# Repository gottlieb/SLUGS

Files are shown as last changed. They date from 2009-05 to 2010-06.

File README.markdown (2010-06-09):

1. Introduction
===============

The Santa Cruz Low-cost UAV GNC System is a high-end UAV Autopilot that has been developed by the Autonomous Systems Lab at the University of California Santa Cruz. It has been thoroughly tested in flight.

SLUGS Official  Website <http://slugsuav.soe.ucsc.edu/>.

The SLUGS Autopilot offers the following features:

* Designed from the ground-up to be easily reprogrammable using Mathworks' Simulink and The Real Time Workshop Embedded Coder.

* Powered by two dsPICs DSCs; one for sensor fusion and attitude estimation from a rich sensor suite. The other for control and communications tasks, providing enough processing power for complex algorithms.

* Small enough to fit in a tactical UAV but able to drive up to ten different servos. It also includes a multiplexer to choose between pilot and automatic control

* Easily go from Simulink simulation to Embedded code. Test your algorithms in Simulink then download them to the Autopilot without any effort.

* Fast execution time. The main processing cycles are executed at 100Hz. Telemetry reports of attitude and position at 100 Hz and the rest of the messages scheduled at 10 Hz.

* Fully integrated with Google Earth to allow the Ground Station operator to create flight way points and display the UAV's flight trajectory in 3D.

* Full featured Ground Station software with graphical displays for all of the UAV telemetry. More than 15 different telemetry sentences to report the full status of the UAV.

* Complete Hardware-In-the-Loop simulator allows you to test new algorithms directly in the auto pilot without leaving your desk. No more waiting for flying to test new ideas.

* Very low power allows to run on a typical RC battery for extended time. You can select to power the receiver and MUX from the same battery, or use an additional battery via configuration jumpers.

* Open. Hardware schematics, layout, and software source code available via a GIT repository with an MIT Open Source License.

2. Code and Hardware
====================

This section will guide you to get the complete repository to your hard drive. If you don't know what GIT is, you can of course read about it in the Wikipedia. This is a small screencast that was prepared for UCSC's Autonomous Systems Lab.

msysgit
--------

Using msysgit is the best way to get Git running on Windows. Git is officially supported under Cygwin, but I consider using it this way more of a hack and I also don't want to install all of Cygwin just for this (takes forever mostly). msysgit can be installed by downloading it from here. Make sure you select the plain Git installation, not the portable or msysgit versions. This is currently at version 1.6.5.1.

There are no surprises during the installation save one set of options. In order for msysgit to work properly with Tortoise Git you must select the option to add Git to the system PATH environment variable (this was the middle option in version 1.6.3).

Once you have msysgit running than all you have to do is open a git bash window (right click on the selected folder on the Windows explorer and select git bash here) and then type:

git clone git://github.com/malife/SLUGS.git

Tar or Zip File
---------------

If you only want a copy of the files and are not interested on getting all the benefits of GIT you can go to the github project page <http://github.com/malife/SLUGS>  and download a zip or tar file of the selected branch by clicking on the `download` button located in the top right corner.

3. Requirements
===============

Software Requirements
---------------------

These are the software requirements to get up and running. Note that if you do not plan on modifying any of the sections you do not need the requirements since we provide binaries for all of the sections. I.E. if you do not want to modify the Ground Station, then you do not need the components listed under that section.
Ground Station 

* Borland C++ Builder 6.0 (old version but very reliable. Yes, hard to find)
* RX Lib for C++ Builder Components (Free)
* Overbyte ICS UDP Components (Free)
* Abakus VCL for graphical components (Commercial)
* Tiny XML for interacting with KML files from Google Earth
* Simulink Models

* Matlab 2007A or newer with Simulink, the Real Time Workshop, and the Embedded Coder
* dsPIC Blockset
* Schematics and Layout

* Version 1 of the board is in Eagle 4.0
* Version 2 of the board in Orcad
* Microchip dsPIC Software and Hardware

* C30 Compiler Student Edition (free)
* PicKit 2 Programmer and Debugger (or any other dsPIC programmer)

Repository Organization
-----------------------
The main Simulink models for each of the DSCs lie in the repository's root directory, they are aptly named ControlMCUSlugsMKII and SensorMCUSlugsMKII. Additionally the repository also includes HEX files of each model.

The root directory also contains an init script (`mcuInit.m`) and a Simulink Library with the most commonly used blocks (`SLUGS_Library.mdl`).

There are eight subdirectories, each with its own README file:

* **Calibration**: It contains all the m-files to produce the magnetometer and accelerometer calibration numbers based on collected data sets. It also contains the temperature compensation scripts.
* **clib**: Contains all the C-files used by Simulink
* **DataSamples**: Self explanatory
* **FlightData**: It contains a script to analyze the collected data from a telemtry file. It also contains a Simulink model to replay the telemetry file.
* **GroundStation**: It contains all the source code of the ground station software.
* **hardware**: It contains all the source, PDFs and Gerbers of the hardware.
* **HILSim**: It contains the Simulink file used for the HIL Simulator.
* **InnerOuterLoop**: It contains the main Simulink file to run software simulation, whic includes a full 6DOF model of the Rascal UAV, the inner and outer loop. It also contains some scripts to analyze the data after every simulation. 

It is important to note that the repository includes a `.gitattributes` file which is used to make Git treat the Simulink model files as binaries (even though they are really text files). This facilitates handling of the MDL files but the tradeoff is that it makes contributions harder. 

Sending a Board to Manufacture
------------------------------

Building a Connection Harness
-----------------------------

(Comment: Remember to point out that the PIC12 should be preprogrammed. Jonathan Lowert)

Flight Harness
--------------

Ground Harness
--------------

Understanding the Architecture
------------------------------

How to Contribute
-----------------

4. Installing Hardware to the UAV

5. Software Simulation

6. Hardware in the Loop Simulation

7. References

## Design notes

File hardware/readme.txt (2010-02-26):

"full_slugs2_and_2_1_with_all_library_pads" contains the full zipped project, library, and padstacks. It contains more files than necessary because I don't want to miss anything. It should work fine.

"board_gerber_files" has the files you need to submit to a board house. It also has some screen shots I made while test-submitting to Sierra Proto Express No-Touch.

"PDFs" has the schematics in PDF form, duh

"link_board" is an Altium Designer 09 project containing schematics for the link board. This board sits between the Xtend radio and the groundstation laptop and acts as a go-between.

Enjoy!

-Greg Horn
August 30, 2009

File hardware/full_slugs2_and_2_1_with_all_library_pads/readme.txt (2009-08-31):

Extract symbols.rar and merge contents with:

C:\OrCAD\OrCAD_16.0\share\pcb\pcb_lib

for library padstacks to work. Override files if necessary.

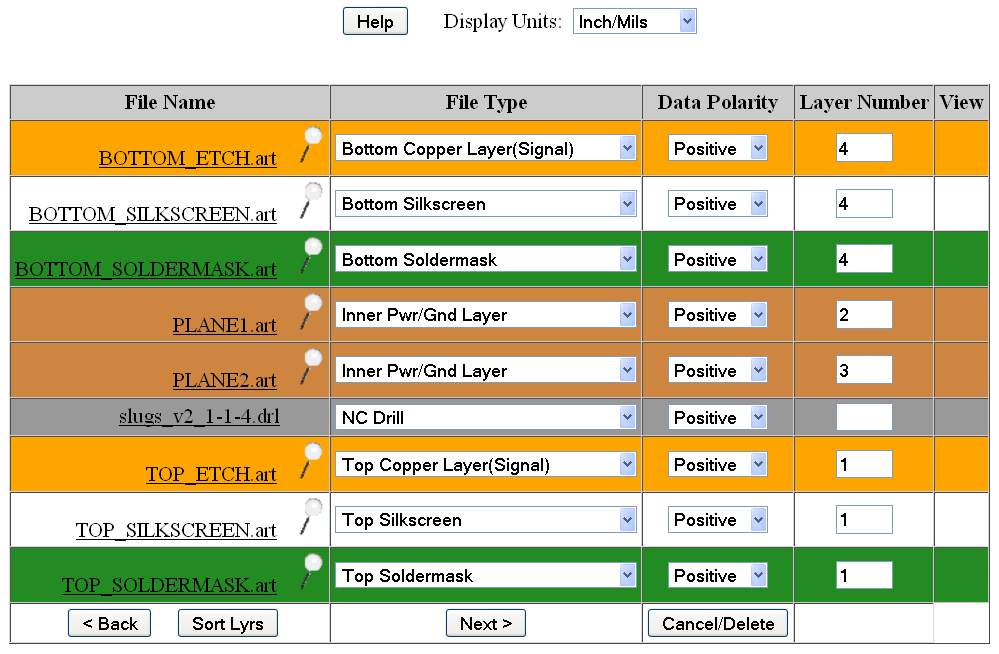
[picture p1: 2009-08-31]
hardware/board_gerber_files/layer_info.bmp

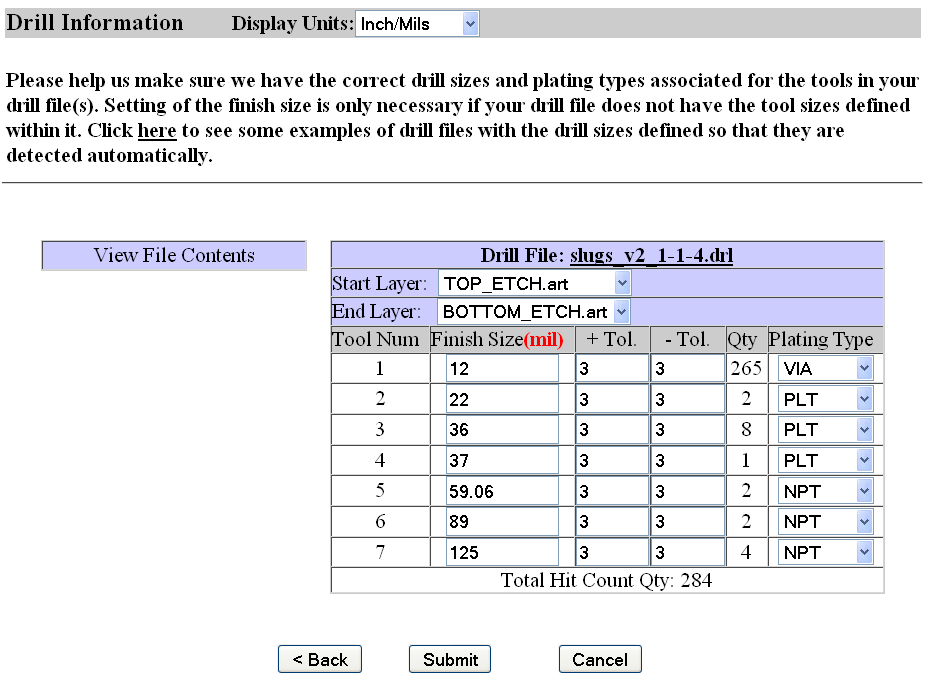
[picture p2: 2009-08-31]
hardware/full_slugs2_and_2_1_with_all_library_pads/SLUGS_V2/allegro_slugs2.1/board_files/drill_info.bmp

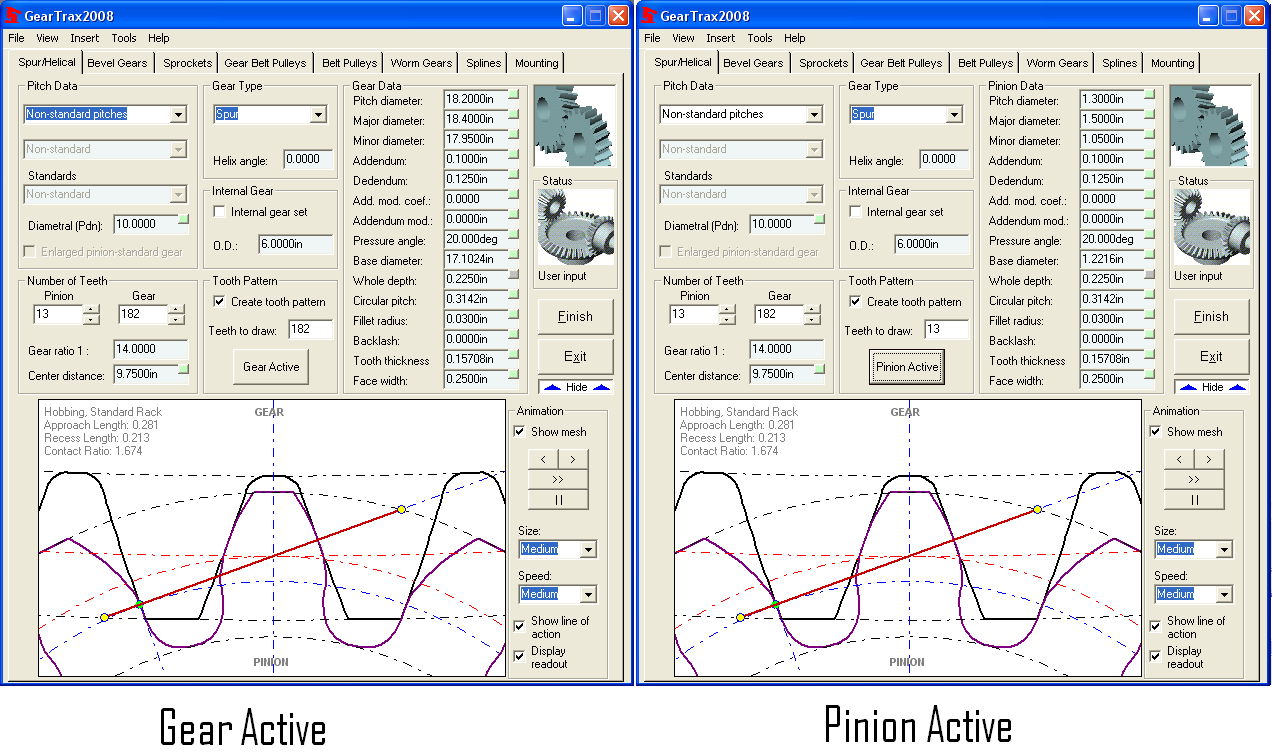
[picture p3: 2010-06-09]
hardware/Rotation Table v3/Gear Specs.bmp

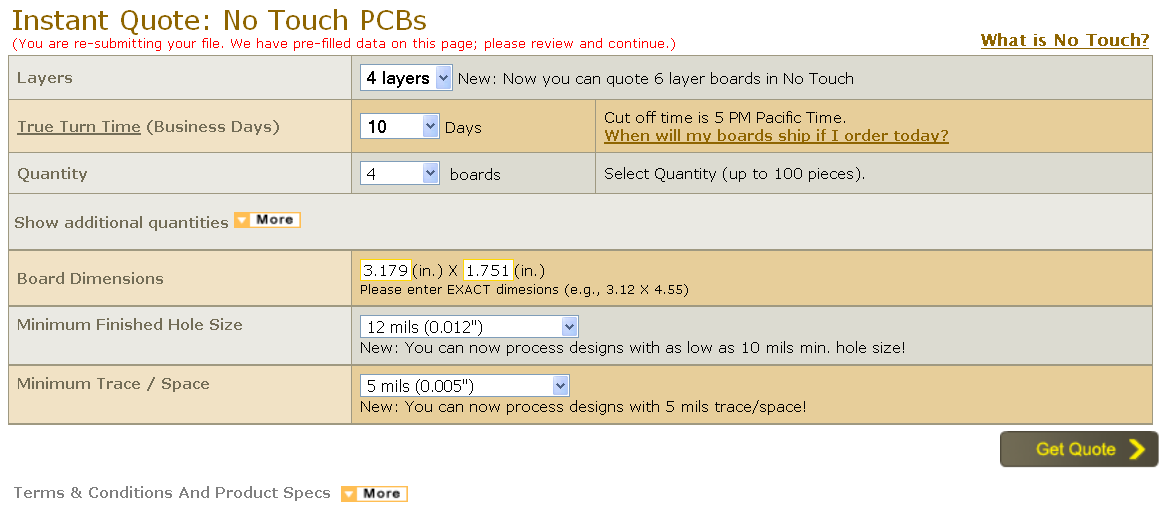
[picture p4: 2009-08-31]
hardware/board_gerber_files/sierra_no_touch_specs.bmp

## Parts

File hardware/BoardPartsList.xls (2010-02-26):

UCSC
BOM: SLUGS 2.1 |  |  |  |  |  |  |  | DNA11120
Date: 11/04/2009 BOM SENT TO THE CUSTOMER
 |  |  |  |  |  |  |  |  |  |  |  |  | N=
Item | SPE part # | Qty/ bd | Reference desig. | Customer part # | Value | Footprint | Voltage Rating | Description / Extended specs | Mnfr or vendor description/ specs | Manfr. | Manf part # | Distributor | Distributor P/N | ASSEMBLY / PROCUREMENT REMARKS | Customer Comments | Alternate Given by customer
1 |  | 34 | C1,C2,C3,C4,C5,C6,C7,C8,C9,C10,C11,C12,C13,C14,C17,C18,C19,C22,C30,C31,C32,C33,C34,C35,C54,C55,C56,C64,C65,C66,C67,C68,C69,C70 |  | .1u | C0603 | 16V |  | CAP .10UF 16V CERAMIC X7R 0603 | Kemet | C0603C104J4RACTU | DIGIKEY | 399-1097-1-ND
2 |  | 10 | C15,C16,C37,C40,C41,C44,C46,C47,C50,C53 |  | 10u | C0805 | 16V |  | CAP CER 10UF 16V X5R 0805 | Taiyo Yuden | EMK212BJ106KG-T | DIGIKEY | 587-1295-1-ND | Ship Date Estimate (mm/dd/yyyy) 1/7/2010 | Replace by alternate | 311-1142-1-ND
3 |  | 7 | C20,C23,C24,C25,C27,C28,C57 |  | 1u | C0603 | 10V |  | CAP 1UF 10V CERAMIC 0603 X5R | Panasonic - ECG | ECJ-1VB1A105K | DIGIKEY | PCC2174CT-ND
4 |  | 1 | C26 |  | 1n | C0603 | 50V |  | CAP 1000PF 50V CERAMIC X7R 0603 | Panasonic - ECG | ECJ-1VB1H102K | DIGIKEY | PCC1772CT-ND
5 |  | 1 | C29 |  | 22u | C1206 |  | 10V (-20%,+80% value tolerance OK) | CAP 22UF 10V CERAMIC F 1206 | Panasonic - ECG | ECJ-3YF1A226Z | DIGIKEY | PCC2236CT-ND
6 |  | 0 | C36,C38 |  | 220u | SMD_CAP_10x10_5 | 25V |  | CAP 220UF 35V ELECT HA SMD | Panasonic - ECG | EEV-HA1V221P | DIGIKEY | PCE3226CT-ND
6 |  | 2 | C36,C38 |  | 220u | SMD_CAP_10x10_5 | 25V |  | CAP 220UF 35V ELECT HA SMD | Panasonic - ECG | EEE-HA1V221P | DIGIKEY | PCE4241CT-ND
7 |  | 1 | C39 |  | 10u,20V | C1206 | 20V |  | CAP TANT 10UF 20V 20% SMD | Kemet | T491A106M020AT | DIGIKEY | 399-5152-1-ND
8 |  | 1 | C49 |  | 4u7 | C0805 | 10V |  | CAP TANTALUM 4.7UF 10V 10% SMD | AVX Corporation | TAJR475K010RNJ | DIGIKEY | 478-3280-1-ND
9 |  | 1 | C52 |  | .22u | C0603 | 16V |  | CAP .22UF 16V CERAMIC Y5V 0603 | Panasonic - ECG | ECJ-1VF1C224Z | DIGIKEY | PCC1790CT-ND
10 |  | 1 | C58 |  | .01u | C0603 | 16V |  | CAP 10000PF 16V CERM X7R 0603 | Panasonic - ECG | ECJ-1VB1C103K | DIGIKEY | PCC1750CT-ND
11 |  | 1 | C59 |  | 2u2 | C0805 | 10V |  | CAP TANTALUM 2.2UF 10V 20% SMD | Rohm Semiconductor | TCFGP1A225M8R | DIGIKEY | 511-1490-1-ND
12 |  | 1 | C60 |  | 470p | C0603 | 50V |  | CAP CERAMIC 470PF 50V NP0 0603 | Panasonic - ECG | ECJ-1VC1H471J | DIGIKEY | PCC2147CT-ND
13 |  | 1 | C61 |  | 47p | C0603 | 50V |  | CAP CERAMIC 47PF 50V NP0 0603 | Yageo | CC0603JRNP09BN470 | DIGIKEY | 311-1065-1-ND
14 |  | 2 | C62,C63 |  | .47u | C0603 | 16V |  | CAP TANT .47UF 16V 10% 0603 | AVX Corporation | TACL474K016RTA | DIGIKEY | 445-1277-1-ND
15 |  | 2 | D1,D2 |  | 1N4148WT | diode_sod523 |  |  | DIODE SWITCH 100V 150MW SOD-523 | Diodes Inc | 1N4148WT-7 | DIGIKEY | 1N4148WTDICT-ND
16 |  | 10 | D5,D6,D7,D8,D9,D10,D11,D12,D13,D14 |  | LED0603 Green | D0603 |  |  | LED 0603 ULTRA BRIGHT GRN 35MCD | Vishay/Semiconductors | TLMG1100-GS08 | DIGIKEY | 751-1165-1-ND
17 |  | 1 | D15 |  | DIODE | dio400 |  |  | DIODE STD REC 1A 50V DO41 | ON Semiconductor | 1N4001RLG | DIGIKEY | 1N4001RLGOSCT-ND
18 |  | 1 | J1 |  | connector_60 | AMPMODU50_60_rightangle |  |  | CONN HEADER 60POS .050" R/A GOLD | Tyco Electronics | 5-104069-7 | DIGIKEY | A31870-ND
19 |  | 2 | J2,J3 |  | GND | jumper2 |  |  |  |  |  |  |  | Ignore. DO NOT MOUNT
20 |  | 1 | J6 |  | BATT | screw_terminal |  |  | TERM BLOCK 2POS SIDE ENT 2.54MM | Tyco Electronics | 282834-2 | DIGIKEY | A98333-ND
21 |  | 1 | R1 |  | 120 | R0603 |  | All resistors 1%, 1/10 watt. | RES 120 OHM 1/10W 1% 0603 SMD | Rohm Semiconductor | MCR03EZPFX1200 | DIGIKEY | RHM120HCT-ND
22 |  | 1 | R2 |  | 120/OPT | R0603 |  |  |  |  |  |  |  | DO NOT MOUNT
23 |  | 2 | R3,R4 |  | 4k7 | R0603 |  |  | RES 4.70K OHM 1/10W 1% 0603 SMD | Rohm Semiconductor | MCR03EZPFX4701 | DIGIKEY | RHM4.70KHCT-ND
24 |  | 2 | R5,R6 |  | 47k | R0603 |  |  | RES 47.0K OHM 1/10W 1% 0603 SMD | Rohm Semiconductor | MCR03EZPFX4702 | DIGIKEY | RHM47.0KHCT-ND
25 |  | 4 | R7,R24,R31,R32 |  | 200 | R0603 |  |  | RES 200 OHM 1/10W 1% 0603 SMD | Rohm Semiconductor | MCR03EZPFX2000 | DIGIKEY | RHM200HCT-ND
26 |  | 4 | R9,R11,R12,R16 |  | 750 | R0603 |  |  | RES 750 OHM 1/10W 1% 0603 SMD | Rohm Semiconductor | MCR03EZPFX7500 | DIGIKEY | RHM750HCT-ND
27 |  | 8 | R10,R13,R14,R15,R17,R18, R19,R20 |  | 5k | R0603 |  |  | RES 4.99K OHM 1/10W 1% 0603 SMD | Rohm Semiconductor | MCR03EZPFX4991 | DIGIKEY | RHM4.99KHCT-ND
29 |  | 1 | R21 |  | 100 | R0603 |  |  | RES 100 OHM 1/10W 1% 0603 SMD | Rohm Semiconductor | MCR03EZPFX1000 | DIGIKEY | RHM100HCT-ND
30 |  | 1 | R22 |  | 13k1,1% | R0603 |  |  | RES 13.0K OHM 1/10W 1% 0603 SMD | Rohm Semiconductor | MCR03EZPFX1302 | DIGIKEY | RHM13.0KHCT-ND
31 |  | 1 | R23 |  | 330k | R0603 |  |  | RES 330K OHM 1/10W 1% 0603 SMD | Rohm Semiconductor | MCR03EZPFX3303 | DIGIKEY | RHM330KHCT-ND
32 |  | 1 | R25 |  | 10k | R0603 |  |  | RES 10.0K OHM 1/10W 1% 0603 SMD | Panasonic - ECG | ERJ-3EKF1002V | DIGIKEY | P10.0KHCT-ND
33 |  | 2 | R26,R28 |  | 17k | R0603 |  |  | RES 16.9K OHM 1/10W 1% 0603 SMD | Panasonic - ECG | ERJ-3EKF1692V | DIGIKEY | P16.9KHCT-ND
34 |  | 1 | R27 |  | 3k3 | R0603 |  |  | RES 3.30K OHM 1/10W 1% 0603 SMD | Rohm Semiconductor | MCR03EZPFX3301 | DIGIKEY | RHM3.30KHCT-ND
35 |  | 2 | R29,R30 |  | 34k | R0603 |  |  | RES 34.0K OHM 1/10W 1% 0603 SMD | Rohm Semiconductor | MCR03EZPFX3402 | DIGIKEY | RHM34.0KHCT-ND
36 |  | 2 | U1,U2 |  | dsPIC33FJ256MC710PT | TQFP100_12x12MC |  |  | IC DSPIC MCU/DSP 256K 100TQFP | Microchip Technology | DSPIC33FJ256MC710-I/PT | DIGIKEY | DSPIC33FJ256MC710-I/PT-ND
37 |  | 2 | U3,U5 |  | SN65HVD230D | d8 |  |  | IC CAN TRANSCEIVER 3.3V 8-SOIC | Texas Instruments | SN65HVD230D | DIGIKEY | SN65HVD230D-ND
38 |  | 1 | U4 |  | ECS2033 | ECS2033 |  |  | OSC 12.000 MHZ 3.3V SMD | ECS Inc | ECS-2033-120-BN | DIGIKEY | XC1426CT-ND
39 |  | 1 | U6 |  | MCP9700 | sot23 |  |  | IC SENSOR THERMAL 2.3V SOT23-3 | Microchip Technology | MCP9700T-E/TT | DIGIKEY | MCP9700T-E/TTCT-ND
40 |  | 1 | U7 |  | 74CBTLV16210 | DGV48 |  |  | IC LV 20-BIT FET BUS SW 48-TVSOP | Texas Instruments | SN74CBTLV16210VR | DIGIKEY | 296-6498-1-ND
41 |  | 0 | U8 |  | MAX3223E | MAX3223EETP |  |  | IC TXRX RS232 250KBPS SD 20-TQFN | Maxim Integrated Products | MAX3223EETP+ | DIGIKEY | MAX3223EETP+-ND
41 |  | 1 | U8 |  | MAX3223E | MAX3223EETP |  |  | IC TXRX RS232 250KBPS SD 20-TQFN | Maxim Integrated Products | MAX3223EETP+ | Maxim Integrated Products | MAX3223EETP+
42 |  | 1 | U9 |  | PIC12F683-XSN | SOIC8-N_MC |  |  | IC MCU FLASH 2KX14 8SOIC | Microchip Technology | PIC12F683-I/SN | DIGIKEY | PIC12F683-I/SN-ND
43 |  | 1 | U10 |  | ptn78000waz | EUT5 |  |  | REG SW 2.5-12.6V 1.5A SMD | Texas Instruments | PTN78000WAZ | DIGIKEY | 296-20508-ND
44 |  | 2 | U11,U12 |  | LP38690SD-3.3 | SDE06A-L |  |  | IC REG LDO 1A 3.3V 6-LLP | National Semiconductor | LP38690SD-3.3/NOPB | DIGIKEY | LP38690SD-3.3CT-ND
45 |  | 1 | U13 |  | LP2986AIMM | MUA08A-L |  |  | IC REG LDO 5V 200MA 8-MSOP | National Semiconductor | LP2986AIMM-5.0/NOPB | DIGIKEY | LP2986AIMM-5.0CT-ND
46 |  | 0 | U14 |  | ADIS16350AMLZ | ADIS16350 |  |  | MOD TRI-AXIS GYRO/ACCEL 24-LEAD | Analog Devices Inc | ADIS16350AMLZ | DIGIKEY | ADIS16350AMLZ-ND
46 |  | 1 | U14 |  | ADIS16350AMLZ | ADIS16350 |  |  | MOD TRI-AXIS GYRO/ACCEL 24-LEAD | SAMTEC | CLM-112-02-L-D | SAMTEC | CLM-112-02-L-D
47 |  | 1 | U15 |  | HMC5843 | HMC5843 |  |  | SENSOR MAGNETIC 3 AXIS 20-LCC | Honeywell Microelectronics & Precision Sensors | HMC5843 | DIGIKEY | 342-1071-ND
48 |  | 1 | U16 |  | LMV844MT | MTC14-L |  |  | IC OP AMP RRIO CMOS INP 14-TSSOP | National Semiconductor | LMV844MT/NOPB | DIGIKEY | LMV844MT-ND
49 |  | 1 | U17 |  | MPXH6115A6U_6T1 | MPXH6115A6U_6T1 |  |  | SENSOR ABS PRESS 16.7PSI MAX | Freescale Semiconductor | MPXH6115A6U | DIGIKEY | MPXH6115A6U-ND
50 |  | 1 | U18 |  | MPXV5004DP | MPXV5010DP |  |  | SENSOR PRESSURE SMD 8-SOP | Freescale Semiconductor | MPXV5004DP | DIGIKEY | MPXV5004DP-ND
51 |  | 1 |  |  |  |  |  | PCB manufactured by SPE |  |  |  |  |  | PCB
 |  | 131 | total # of components
 |  | 140 | Total # of compnents to be assembled
 |  | 1 | total # of DNP components
 |  | 3 | total # of DIP components to be Assembled
 |  | 137 | total # of SMD components to be Assembled

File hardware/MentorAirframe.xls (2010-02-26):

Price List
Description | Qty | Price | Total | Web Page
Multiplex Mentor | 2 | 147.99 | 295.98 | http://www3.towerhobbies.com/cgi-bin/wti0001p?&I=LXVEP7
Multiplex Mentor servo pack | 2 | 69.9 | 139.8 | http://www3.towerhobbies.com/cgi-bin/wti0001p?&I=LXVEP9&P=M
Phoenix 60 ESC | 2 | 118.99 | 237.98 | http://www3.towerhobbies.com/cgi-bin/wti0001p?&I=LXGVS3&P=FR
Castle Creations Link Programming Kit | 1 | 21.99 | 21.99 | http://www3.towerhobbies.com/cgi-bin/wti0001p?&I=LXGVR8&P=7
Himax 3528-1000 Mentor Motor | 2 | 147.99 | 295.98 | http://www3.towerhobbies.com/cgi-bin/wti0001p?&I=LXVEP8&P=M
APC 11 x 7 Sport Propeller | 5 | 2.79 | 13.95 | http://www3.towerhobbies.com/cgi-bin/wti0001p?&I=LX1558&P=M
WS Deans 2-pin Ultra Plug | 15 | 3.09 | 46.35 | http://www3.towerhobbies.com/cgi-bin/wti0001p?&I=LXKX39&P=M
CA+ Glue | 2 | 6.99 | 13.98 | http://www3.towerhobbies.com/cgi-bin/wti0001p?&I=LXK287&P=ML
Spektrum DX7 with AR7000 | 1 | 349.99 | 349.99 | http://search.horizonhobby.com/index.jsp?N=0&Ntt=dx7&sid=126B91FA82E5
Thunder Power 1350 ma 3-cell Pro Lite V2 | 3 | 34.99 | 104.97 | http://www.horizonhobby.com/Products/Default.aspx?ProdID=THP13503SPL2
Thunder Power 5000ma 3-cell Pro Power | 3 | 129.99 | 389.97 | http://www.horizonhobby.com/Products/Default.aspx?ProdID=THP50003SP30
Spektrum AR7000 DSM2 | 1 | 99.99 | 99.99 | http://www.horizonhobby.com/Products/Default.aspx?ProdID=SPM6070
Thunder Power LiPo Charger and Balancer | 1 | 99.99 | 99.99 | http://www.horizonhobby.com/Products/Default.aspx?ProdID=THP610
 |  |  | 0
 |  |  | 0
 |  |  | 0
 |  |  | 0
 |  |  | 0
 | TOTAL |  | 2110.92

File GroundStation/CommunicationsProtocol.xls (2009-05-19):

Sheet: Sentence Structure
SYNC1 | SYNC2 | TYPE | LENGTH | PAYLOAD |  |  |  | EOM1 | EOM2 | CHKSM | General Structure
$ | @ | 1 | 27 | 80 | 1 | … | 35 | * | @ | 241 | Sample Sentence
 |  |  |  |  |  |  |  |  |  |  |  |  |  | 201
Message Identifiers |  |  |  |  |  |  |  |  |  |  |  | Memory Locations
Type | Payload Length | Contents |  |  |  |  |  |  |  | Update Freq. |  | Address | Contents | Message
SENSOR MCU GENERATED SENTENCES |  |  |  |  |  |  |  |  |  |  |  | 0 | PID 1 P Gain | PID Longitudinal Gains
1 | 27 | GPS Data from Messages GPRMC and GPGGA |  |  |  |  |  |  |  | 10 |  | 2 | PID 1 I Gain
2 | 4 | MCU Status: Load, Vdetect, Battery Status |  |  |  |  |  |  |  | 10 |  | 4 | PID 1 D Gain
3 | 18 | Raw sensor reading from the sensors |  |  |  |  |  |  |  | 10 |  | 6 | PID 2 P Gain
4 | 24 | Attitude Estimation from Kalman Filter |  |  |  |  |  |  |  | 100 |  | 8 | PID 2 I Gain
5 | 10 | Dynamic and Static Pressure, Temperature |  |  |  |  |  |  |  | 10 |  | 10 | PID 2 D Gain
6 | 24 | Sensor Bias |  |  |  |  |  |  |  | 10 |  | 12 | PID 3 P Gain
7 | 18 | Diagnostic Message |  |  |  |  |  |  |  | 10 |  | 14 | PID 3 I Gain
8 |  | Vacant |  |  |  |  |  |  |  |  |  | 16 | PID 3 D Gain
9 | 10 | Pilot Console Commands |  |  |  |  |  |  |  | 10 |  | 18 | PID 4 P Gain
10 |  | Vacant |  |  |  |  |  |  |  |  |  | 20 | PID 4 I Gain
11 | 24 | XYZ Data |  |  |  |  |  |  |  | 100 |  | 22 | PID 4 D Gain
12 |  | Vacant 2 |  |  |  |  |  |  |  |  |  | 24 | PID 5 P Gain
13 |  | Vacant 3 |  |  |  |  |  |  |  |  |  | 26 | PID 5 I Gain
14 |  | Vacant 4 |  |  |  |  |  |  |  |  |  | 28 | PID 5 D Gain
15 |  | Vacant 5 |  |  |  |  |  |  |  |  |  | 30 | PID 6 P Gain | PID Lateral Gains
CONTROL MCU GENERATED SENTENCES |  |  |  |  |  |  |  |  |  |  |  | 32 | PID 6 I Gain
100 | 20 | PWM Commands |  |  |  |  |  |  |  | 10 |  | 34 | PID 6 D Gain
101 | 20 | AP Status |  |  |  |  |  |  |  | 10 |  | 36 | PID 7 P Gain
102 | 17 | Calibration Report |  |  |  |  |  |  |  | OD |  | 38 | PID 7 I Gain
103 |  | Vacant |  |  |  |  |  |  |  |  |  | 40 | PID 7 D Gain
104 |  | Vacant |  |  |  |  |  |  |  |  |  | 42 | PID 8 P Gain
105 | 5 | Aknowledge Message |  |  |  |  |  |  |  | OD |  | 44 | PID 8 I Gain
106 |  | Vacant |  |  |  |  |  |  |  |  |  | 46 | PID 8 D Gain
GROUND STATION GENERATED SENTENCES |  |  |  |  |  |  |  |  |  |  |  | 48 | PID 9 P Gain
200 | 7 | Control surfaces calibration |  |  |  |  |  |  |  | OD |  | 50 | PID 9 I Gain
201 | 16 | Waypoint Config |  |  |  |  |  |  |  | OD |  | 52 | PID 9 D Gain
202 | 13 | PIDCalibration Values |  |  |  |  |  |  |  | OD |  | 54 | PID 10 P Gain
203 |  | Vacant |  |  |  |  |  |  |  | OD |  | 56 | PID 10 I Gain
204 | 10 | Query AP Info |  |  |  |  |  |  |  | OD |  | 58 | PID 10 D Gain
205 | 1 | HIL Simulator On |  |  |  |  |  |  |  | OD |  | 60 | WP1 Lat | Waypoint Config | 2
206 | 7 | Commands to AP |  |  |  |  |  |  |  | OD |  | 62 | WP1 Long |  | 2
207 | 10 | Change AP Status |  |  |  |  |  |  |  | OD |  | 64 | WP1 Height |  | 2
 |  |  |  |  |  |  |  |  |  |  |  | 66 | WP1 Type |  | 1
 |  |  |  |  |  |  |  |  |  |  |  | 67 | WP1 Value |  | 1
 |  |  |  |  |  |  |  |  |  |  |  | 68 | WP2 Lat |  | 2
 |  |  |  |  |  |  |  |  |  |  |  | 70 | WP2 Long |  | 2
 |  |  |  |  |  |  |  |  |  |  |  | 72 | WP2 Height |  | 2
 |  |  |  |  |  |  |  |  |  |  |  | 74 | WP2 Type |  | 1
 |  |  |  |  |  |  |  |  |  |  |  | 75 | WP2 Value |  | 1
 |  |  |  |  |  |  |  |  |  |  |  | 76 | WP3 Lat |  | 2
 |  |  |  |  |  |  |  |  |  |  |  | 78 | WP3 Long |  | 2
 |  |  |  |  |  |  |  |  |  |  |  | 80 | WP3 Height |  | 2
 |  |  |  |  |  |  |  |  |  |  |  | 82 | WP3 Type |  | 1
 |  |  |  |  |  |  |  |  |  |  |  | 83 | WP3 Value |  | 1
 |  |  |  |  |  |  |  |  |  |  |  | 84 | WP4 Lat |  | 2
 |  |  |  |  |  |  |  |  |  |  |  | 86 | WP4 Long |  | 2
 |  |  |  |  |  |  |  |  |  |  |  | 88 | WP4 Height |  | 2
 |  |  |  |  |  |  |  |  |  |  |  | 90 | WP4 Type |  | 1
 |  |  |  |  |  |  |  |  |  |  |  | 91 | WP4 Value |  | 1
 |  |  |  |  |  |  |  |  |  |  |  | 92 | WP5 Lat |  | 2
 |  |  |  |  |  |  |  |  |  |  |  | 94 | WP5 Long |  | 2
 |  |  |  |  |  |  |  |  |  |  |  | 96 | WP5 Height |  | 2
 |  |  |  |  |  |  |  |  |  |  |  | 98 | WP5 Type |  | 1
 |  |  |  |  |  |  |  |  |  |  |  | 99 | WP5 Value |  | 1
 |  |  |  |  |  |  |  |  |  |  |  | 100 | WP6 Lat |  | 2
 |  |  |  |  |  |  |  |  |  |  |  | 102 | WP6 Long |  | 2
 |  |  |  |  |  |  |  |  |  |  |  | 104 | WP6 Height |  | 2
 |  |  |  |  |  |  |  |  |  |  |  | 106 | WP6 Type |  | 1
 |  |  |  |  |  |  |  |  |  |  |  | 107 | WP6 Value |  | 1
 |  |  |  |  |  |  |  |  |  |  |  | 108 | WP7 Lat |  | 2
 |  |  |  |  |  |  |  |  |  |  |  | 110 | WP7 Long |  | 2
 |  |  |  |  |  |  |  |  |  |  |  | 112 | WP7 Height |  | 2
 |  |  |  |  |  |  |  |  |  |  |  | 114 | WP7 Type |  | 1
 |  |  |  |  |  |  |  |  |  |  |  | 115 | WP7 Value |  | 1
 |  |  |  |  |  |  |  |  |  |  |  | 116 | WP8 Lat |  | 2
 |  |  |  |  |  |  |  |  |  |  |  | 118 | WP8 Long |  | 2
 |  |  |  |  |  |  |  |  |  |  |  | 120 | WP8 Height |  | 2
 |  |  |  |  |  |  |  |  |  |  |  | 122 | WP8 Type |  | 1
 |  |  |  |  |  |  |  |  |  |  |  | 123 | WP8 Value |  | 1
 |  |  |  |  |  |  |  |  |  |  |  | 124 | WP9 Lat |  | 2
 |  |  |  |  |  |  |  |  |  |  |  | 126 | WP9 Long |  | 2
 |  |  |  |  |  |  |  |  |  |  |  | 128 | WP9 Height |  | 2
 |  |  |  |  |  |  |  |  |  |  |  | 130 | WP9 Type |  | 1
 |  |  |  |  |  |  |  |  |  |  |  | 131 | WP9 Value |  | 1
 |  |  |  |  |  |  |  |  |  |  |  | 132 | WP10 Lat |  | 2
 |  |  |  |  |  |  |  |  |  |  |  | 134 | WP10 Long |  | 2
 |  |  |  |  |  |  |  |  |  |  |  | 136 | WP10 Height |  | 2
 |  |  |  |  |  |  |  |  |  |  |  | 138 | WP10 Type |  | 1
 |  |  |  |  |  |  |  |  |  |  |  | 139 | WP10 Value |  | 1
 |  |  |  |  |  |  |  |  |  |  |  | 140 | GS Location Lat | GS Location | 2
 |  |  |  |  |  |  |  |  |  |  |  | 142 | GS Location Long |  | 2
 |  |  |  |  |  |  |  |  |  |  |  | 144 | GS Location Height |  | 2
 |  |  |  |  |  |  |  |  |  |  |  | 146 | GS Location Type |  | 1
 |  |  |  |  |  |  |  |  |  |  |  | 147 | GS Location Value |  | 1
 |  |  |  |  |  |  |  |  |  |  |  |  |  | Ground Station Location
 |  |  |  |  |  |  |  |  |  |  |  |  | L Elevator Positive Limit | Control Surface Limits
 |  |  |  |  |  |  |  |  |  |  |  |  | L Elevator Negative Limit
 |  |  |  |  |  |  |  |  |  |  |  |  | R Elevator Positive Limit
 |  |  |  |  |  |  |  |  |  |  |  |  | R Elevator Negative Limit
 |  |  |  |  |  |  |  |  |  |  |  |  | L Aileron Positive Limit
 |  |  |  |  |  |  |  |  |  |  |  |  | L Aileron Negative Limit
 |  |  |  |  |  |  |  |  |  |  |  |  | R Aileron Positive Limit
 |  |  |  |  |  |  |  |  |  |  |  |  | R Aileron Negative Limit
 |  |  |  |  |  |  |  |  |  |  |  |  | L Flap Positive Limit
 |  |  |  |  |  |  |  |  |  |  |  |  | L Flap Negative Limit
 |  |  |  |  |  |  |  |  |  |  |  |  | R Flap Positive Limit
 |  |  |  |  |  |  |  |  |  |  |  |  | R Flap Negative Limit
 |  |  |  |  |  |  |  |  |  |  |  |  | Rudder Positive Limit
 |  |  |  |  |  |  |  |  |  |  |  |  | Rudder Negative Limit
 |  |  |  |  |  |  |  |  |  |  |  |  | Throttle Positive Limit
 |  |  |  |  |  |  |  |  |  |  |  |  | Throttle Negative Limit
 |  |  |  |  |  |  |  |  |  |  |  |  | AUX1 Positive Limit
 |  |  |  |  |  |  |  |  |  |  |  |  | AUX1 Negative Limit
 |  |  |  |  |  |  |  |  |  |  |  |  | AUX2 Positive Limit
 |  |  |  |  |  |  |  |  |  |  |  |  | AUX2 Negative Limit
 |  |  |  |  |  |  |  |  |  |  |  |  | L Elev Max | Control Surfaces Calibration Table NOE: Max and Min are 10 degrees (pos and neg) for calibration purposes, except for throttle
 |  |  |  |  |  |  |  |  |  |  |  |  | L Elev Middle
 |  |  |  |  |  |  |  |  |  |  |  |  | L Elev Min
 |  |  |  |  |  |  |  |  |  |  |  |  | R Elev Max
 |  |  |  |  |  |  |  |  |  |  |  |  | R Elev Middle
 |  |  |  |  |  |  |  |  |  |  |  |  | R Elev Min
 |  |  |  |  |  |  |  |  |  |  |  |  | L Aileron Max
 |  |  |  |  |  |  |  |  |  |  |  |  | L Aileron Middle
 |  |  |  |  |  |  |  |  |  |  |  |  | L Aileron Min
 |  |  |  |  |  |  |  |  |  |  |  |  | R Aileron Max
 |  |  |  |  |  |  |  |  |  |  |  |  | R Aileron Middle
 |  |  |  |  |  |  |  |  |  |  |  |  | R Aileron Min
 |  |  |  |  |  |  |  |  |  |  |  |  | L Flap Max
 |  |  |  |  |  |  |  |  |  |  |  |  | L Flap Middle
 |  |  |  |  |  |  |  |  |  |  |  |  | L Flap Min
 |  |  |  |  |  |  |  |  |  |  |  |  | R Flap Max
 |  |  |  |  |  |  |  |  |  |  |  |  | R Flap Middle
 |  |  |  |  |  |  |  |  |  |  |  |  | R Flap Min
 |  |  |  |  |  |  |  |  |  |  |  |  | Rudder Max
 |  |  |  |  |  |  |  |  |  |  |  |  | Rudder Middle
 |  |  |  |  |  |  |  |  |  |  |  |  | Rudder Min
 |  |  |  |  |  |  |  |  |  |  |  |  | Throttle Max
 |  |  |  |  |  |  |  |  |  |  |  |  | Throttle Middle
 |  |  |  |  |  |  |  |  |  |  |  |  | Throttle Min
 |  |  |  |  |  |  |  |  |  |  |  |  | AUX 1 Max
 |  |  |  |  |  |  |  |  |  |  |  |  | AUX 1 Middle
 |  |  |  |  |  |  |  |  |  |  |  |  | AUX 1 Min
 |  |  |  |  |  |  |  |  |  |  |  |  | AUX 2 Max
 |  |  |  |  |  |  |  |  |  |  |  |  | AUX 2 Middle
 |  |  |  |  |  |  |  |  |  |  |  |  | AUX 2 Min

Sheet: GPS Data
Pos Start | Byte Count | Type | Contents
0 | 1 | U Char | Year
1 | 1 | U Char | Month
2 | 1 | U Char | Day
3 | 1 | U Char | Hour
4 | 1 | U Char | Min
5 | 1 | U Char | Sec
6 | 4 | float | Latitude in degrees
10 | 4 | float | Longitude in Degrees
14 | 4 | float | Height in Degrees
18 | 2 | short | Course over ground
20 | 2 | short | Speed over Ground
22 | 2 | short | Horizontal Dillusion of Precision
24 | 1 | U Char | Fix?
25 | 1 | U Char | Satellites in view
26 | 1 | U Char | New Data

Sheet: MCU Status
Pos Start | Byte Count | Type | Contents
0 | 1 | U Char | MCU Load
1 | 1 | U Char | Vdetect Flag
2 | 2 | short | Battery voltage in millivolts

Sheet: Raw Sensor
Pos Start | Byte Count | Type | Contents
0 | 2 | short | Gyro X
2 | 2 | short | Gyro Y
4 | 2 | short | Gyro Z
6 | 2 | short | Accel X
8 | 2 | short | Accel Y
10 | 2 | short | Accel Z
12 | 2 | short | Mag X
14 | 2 | short | Mag Y
16 | 2 | short | Mag Z

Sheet: Attitude
Pos Start | Byte Count | Type | Contents
0 | 4 | float | Roll
4 | 4 | float | Pitch
8 | 4 | float | Yaw
12 | 4 | float | P
16 | 4 | float | Q
20 | 4 | float | R

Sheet: Dynamic
Pos Start | Byte Count | Type | Contents
0 | 4 | float | Dynamic Pressure (Pa)
4 | 4 | float | Static Pressure (Pa)
8 | 2 | short | Temperature ( C )

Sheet: Sensor Bias
Pos Start | Byte Count | Type | Contents
0 | 4 | float | Accel X Bias
4 | 4 | float | Accel Y Bias
8 | 4 | float | Accel Z Bias
12 | 4 | float | Gyro X Bias
16 | 4 | float | Gyro Y Bias
20 | 4 | float | Gyro Z Bias

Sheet: Diagnostic
Pos Start | Byte Count | Type | Contents
0 | 4 | float | Diagnostic 1
4 | 4 | float | Diagnostic 2
8 | 4 | float | Diagnostic 3
12 | 2 | Short | Diagnostic 4
14 | 2 | Short | Diagnostic 5
16 | 2 | Short | Diagnostic 6

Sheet: XYZ Data
Pos Start | Byte Count | Type | Contents
0 | 4 | float | X in meters WRT GS
4 | 4 | float | Y in meters WRT GS
8 | 4 | float | Z in meters WRT GS
12 | 4 | float | VX in m/s
16 | 4 | float | VY in m/s
20 | 4 | float | VZ in m/s

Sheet: Aknowledge Msg
Pos Start | Byte Count | Type | Contents
0 | 1 | uchar | WP Aknowledge
4 | 1 | uchar | Control Surface akn
8 | 1 | uchar | PID Akn
12 | 1 | uchar | Limits Akn
16 | 1 | uchar | FilOnOf Akn

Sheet: Pilot Console
Pos Start | Byte Count | Type | Contents
0 | 2 | short | Throttle
2 | 2 | short | Left Aileron
4 | 2 | short | Right Aileron
6 | 2 | short | Rudder
8 | 2 | short | Elevator

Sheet: PWM Commands
Pos Start | Byte Count | Type | Contents
0 | 2 | short | Throttle
2 | 2 | short | Left Aileron
4 | 2 | short | Right Aileron
6 | 2 | short | Rudder
8 | 2 | short | Left Elevator
10 | 2 | short | Right Elevator
12 | 2 | short | Left Flap
14 | 2 | short | Right Flap
16 | 2 | short | Aux 1
18 | 2 | short | Aux 2

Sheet: PID Config
Pos Start | Byte Count | Type | Contents
0 | 1 | char | PID Loop ID
1 | 4 | float | P Gain
5 | 4 | float | I Gain
9 | 4 | float | D Gain

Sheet: Calib Report
Pos Start | Byte Count | Type | Contents
0 | 1 | char | Report ID | 1 | PID Gains
1 | 1 | char | Index | 2 | WP
2 | 4 | float | Value 1 | 3 | Pass trhough status | Note: In type 3 char mapping is | Pos Start | Byte Count | Type | Contents
6 | 4 | flaot | Value 2 | 4 | Command | as follows: | 0 | 1 | char | Report ID
10 | 4 | float | Value 3 |  |  |  | 1 | 1 | char | dt_pass
14 | 1 | char | value type | used for waypoints |  |  | 2 | 4 | char | dla_pass
15 | 2 | short | value for type | used for waypoints |  |  | 3 | 4 | char | dra_pass
 |  |  |  |  |  |  | 4 | 4 | char | dr_pass
 | 17 |  |  |  |  |  | 5 | 1 | char | dle_pass
 |  |  |  |  |  |  | 6 | 11 | char | vacant
 |  |  |  |  |  | Note: In type 4 the index corresponds to
 |  |  |  |  |  | the control type as described in message 206

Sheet: Query Ap Info
Pos Start | Byte Count | Type | Contents
0 | 1 | char | Report ID Required | 1 | PID Gains
1 | 1 | char | ID Index Required | 2 | WP Config
2 | 8 | char | Vacant | 3 | Control Surface Passthrough
 |  |  |  | 4 | Command

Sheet: WP Config
Pos Start | Byte Count | Type | Contents
0 | 1 | char | WayPoint ID
1 | 4 | float | Lat
5 | 4 | flaot | Long
9 | 4 | float | H | 1 | Regular WP
13 | 1 | char | WayPoint Type | 2 | Orbital WP
14 | 2 | short | Value for Type
 | 16

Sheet: AP Status
Pos Start | Byte Count | Type | Contents
0 | 1 | char | control Type | 1 | Manual
1 | 1 | char | beacon status | 2 | AP Direct Commands
2 | 1 | char | HIL Status | 3 | AP Way Point Nav
3 | 17 | char | Vacant | 4 | Passthrough
 |  |  |  | 5 | Selective Pass from Pilot
 |  |  |  | 6 | Selective Pass from AP
 | 20

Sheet: Commands2AP
Pos Start | Byte Count | Type | Contents
0 | 1 | char | Command Type | 1 | Height
1 | 4 | float | Value 1 | 2 | Turn Rate
5 | 4 | float | Value 2 | 3 | Airspeed
9 | 1 | char | Value 3 | 4 | Got to WP
 | 10

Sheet: ChangeAP Status
Pos Start | Byte Count | Type | Contents
0 | 1 | char | NewStatus | 1 | Manual
1 | 1 | char | Value 1 | 2 | AP Direct Commands
2 | 1 | char | Value 2 | 3 | AP Way Point Nav
3 | 1 | char | Value 3 | 4 | Passthrough
4 | 1 | char | Value 4 | 5 | Selective Pass from Pilot
5 | 1 | char | Value 5 | 6 | Selective Pass from AP
6 | 1 | char | Value 6
7 | 1 | char | Value 7
8 | 1 | char | Value 8
 | 9

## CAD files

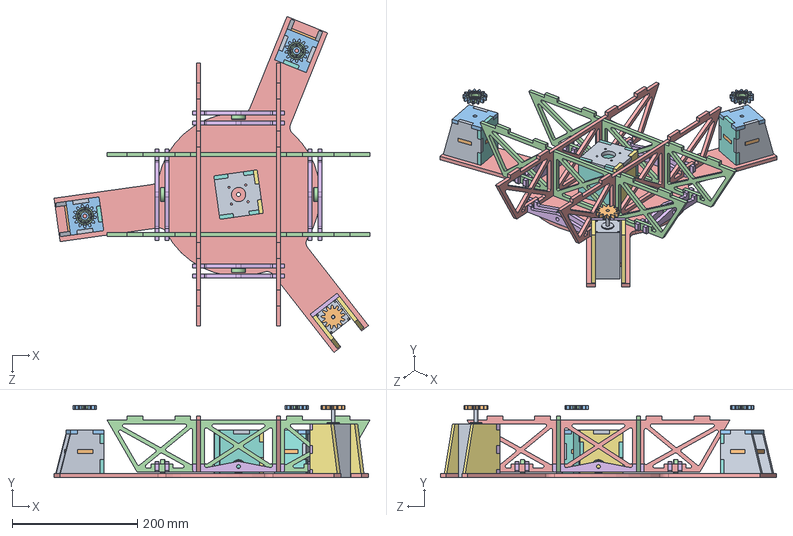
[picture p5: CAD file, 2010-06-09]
hardware/Rotation Table v3/Assembly.SLDASM
503.7 x 115.1 x 535.6 mm
pittmanservo
Pinion
support Pinion x 2
Instrument Ball Bearing_AI x 6
base plate
motor mount plate
motor mount support x 2
support pinion mount front x 2
support pinion mount lateral x 4
support pinion mount center x 2
support pinion mount top x 2
base truss 1 x 2
base truss 2 x 2
bearing stand v2 x 8
spindle mount front
spindle mount lateral x 2
spindle mount top

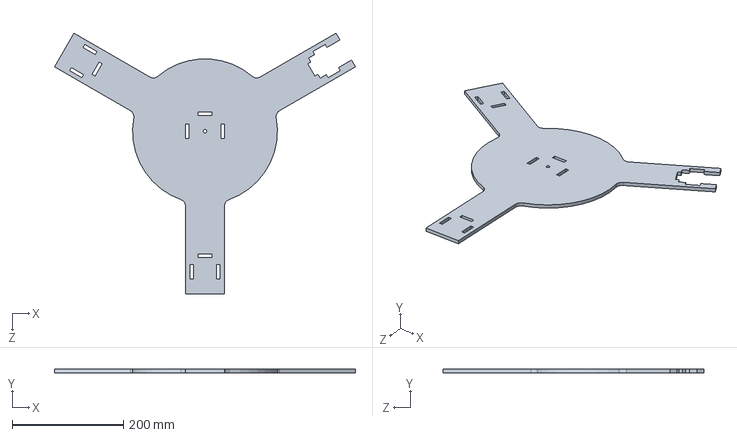
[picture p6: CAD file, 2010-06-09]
hardware/Rotation Table v3/base plate.SLDPRT
540.9 x 6.35 x 468.4 mm

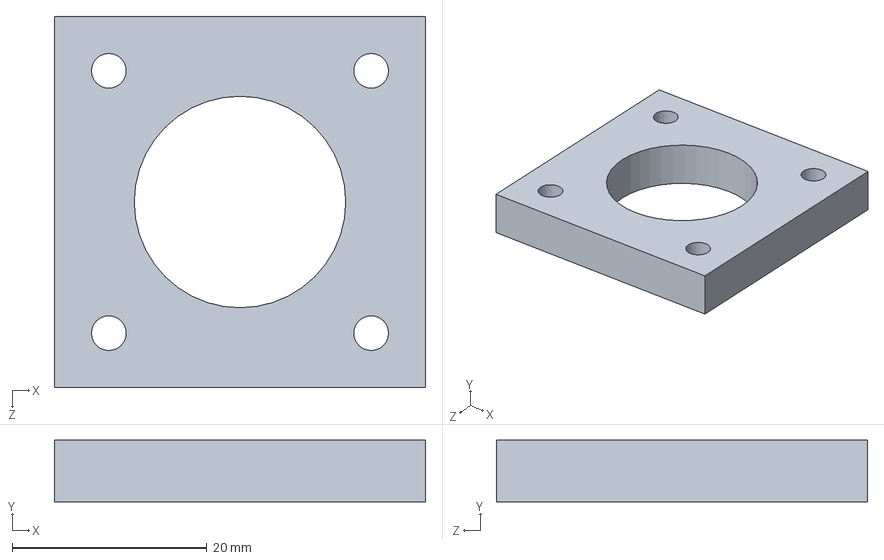
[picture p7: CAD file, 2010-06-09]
hardware/Rotation Table v3/bearing sleeve.SLDPRT
38.1 x 6.35 x 38.1 mm

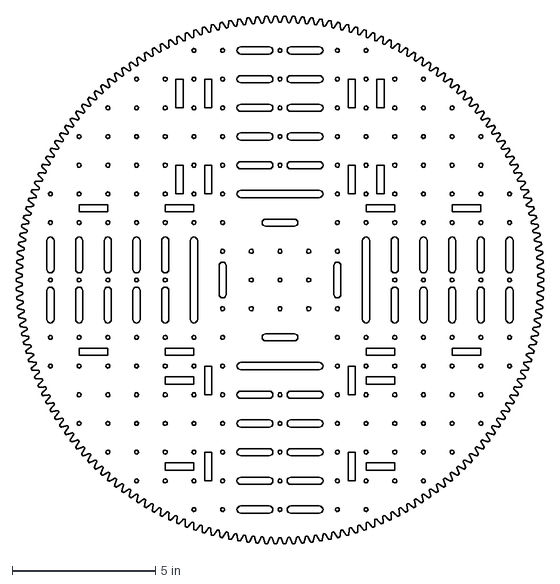
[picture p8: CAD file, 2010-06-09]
hardware/Rotation Table v3/parts2.DXF
18.4 x 18.4 in

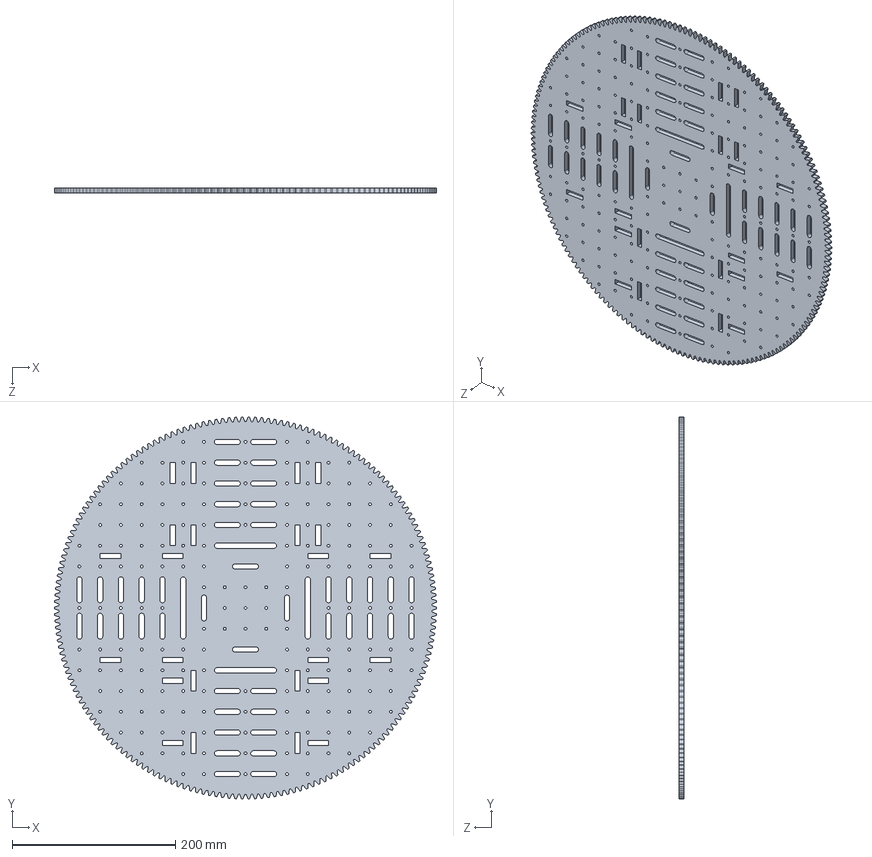
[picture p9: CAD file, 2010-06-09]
hardware/Rotation Table v3/Table gear alternative.SLDPRT
467.4 x 467.3 x 6.35 mm

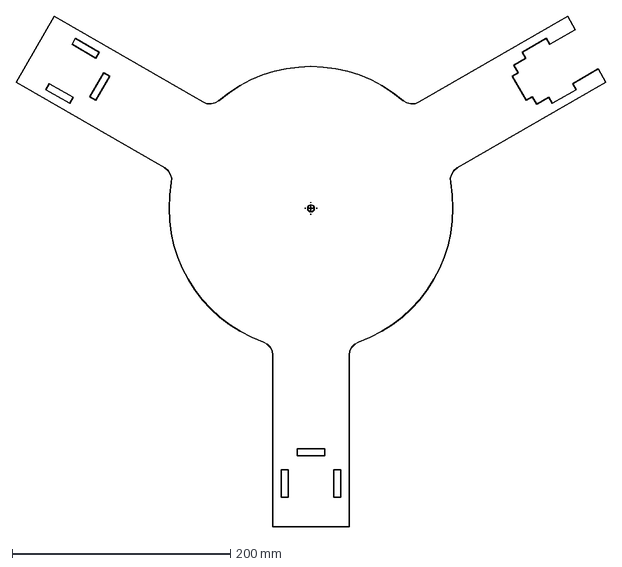
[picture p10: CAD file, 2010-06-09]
hardware/Rotation Table v3/base plate last version.DXF
540.9 x 468.4 mm

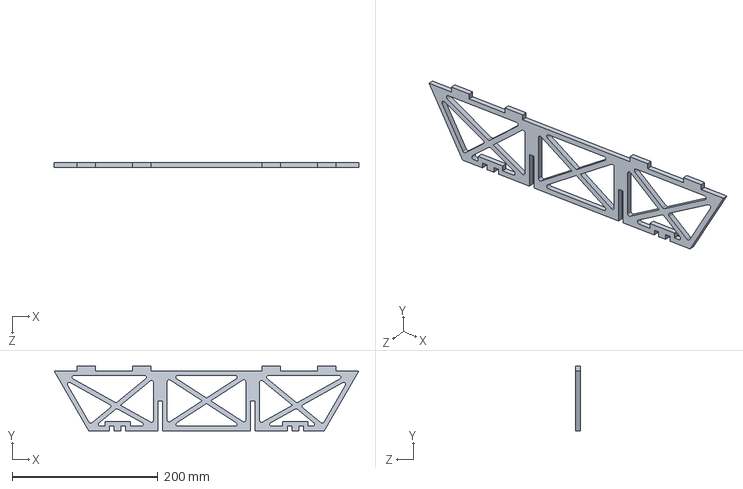
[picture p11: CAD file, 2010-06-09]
hardware/Rotation Table v3/base truss 2.SLDPRT
419.1 x 88.9 x 6.35 mm

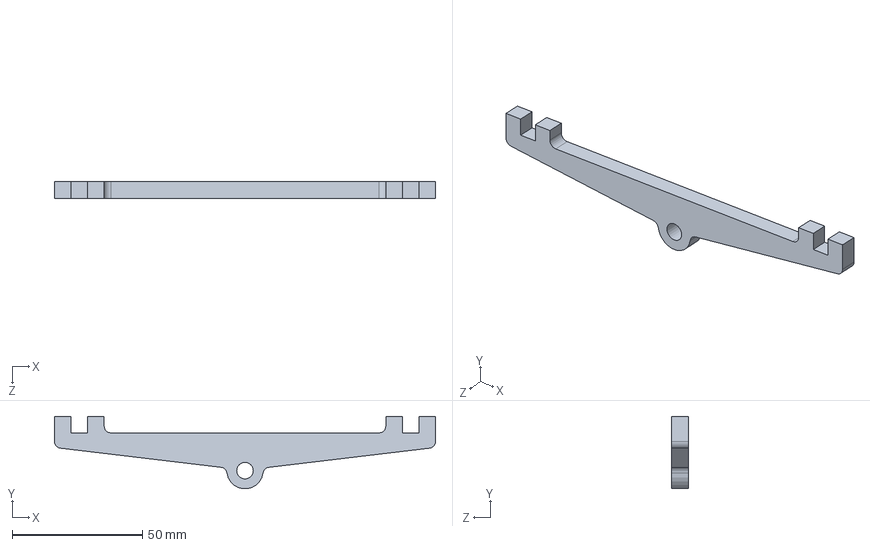
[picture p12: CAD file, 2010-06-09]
hardware/Rotation Table v3/bearing stand.SLDPRT
146.1 x 27.8 x 6.35 mm

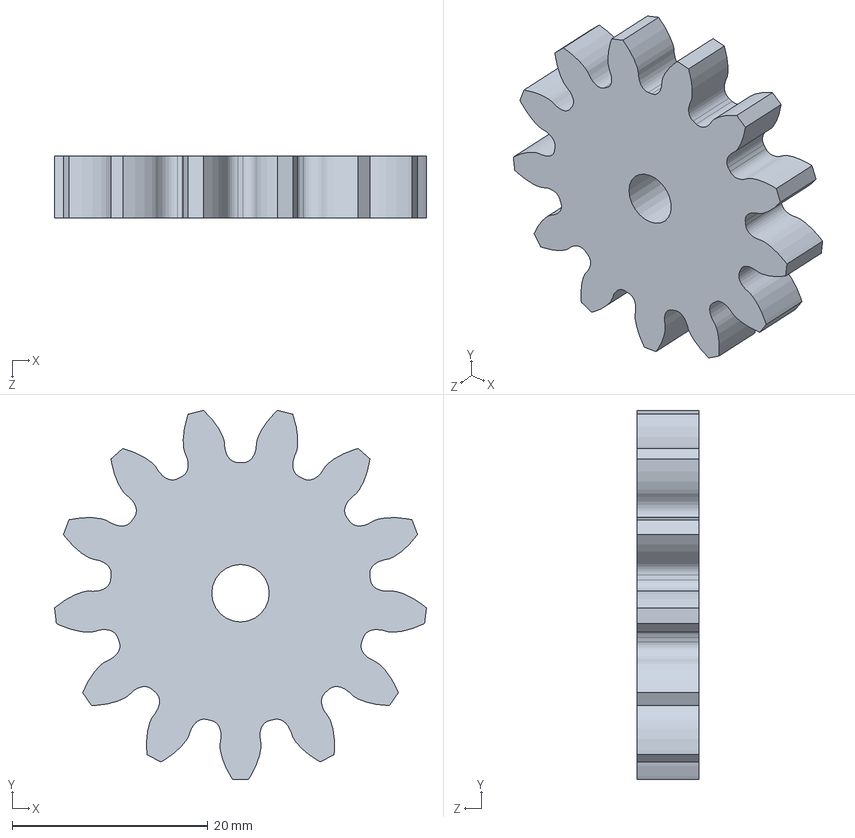
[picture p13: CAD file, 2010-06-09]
hardware/Rotation Table v3/Pinion.SLDPRT
38.0 x 37.7 x 6.35 mm

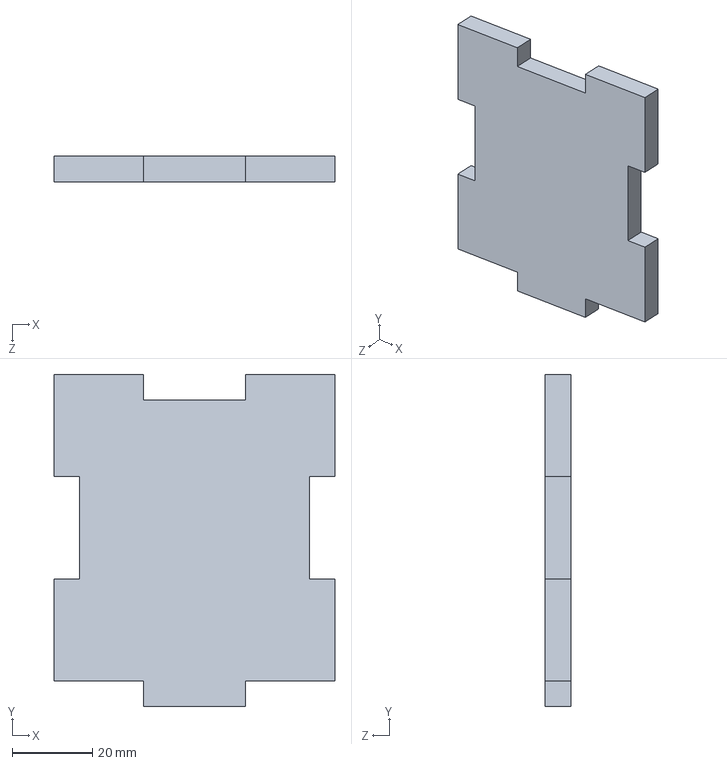
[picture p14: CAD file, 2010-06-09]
hardware/Rotation Table v3/spindle mount front.SLDPRT
69.8 x 82.5 x 6.35 mm

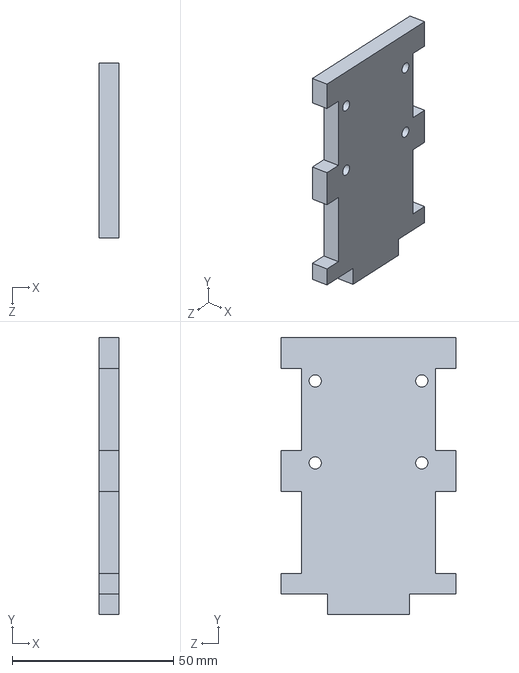
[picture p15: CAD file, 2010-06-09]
hardware/Rotation Table v3/motor mount plate.SLDPRT
6.35 x 85.9 x 54.4 mm

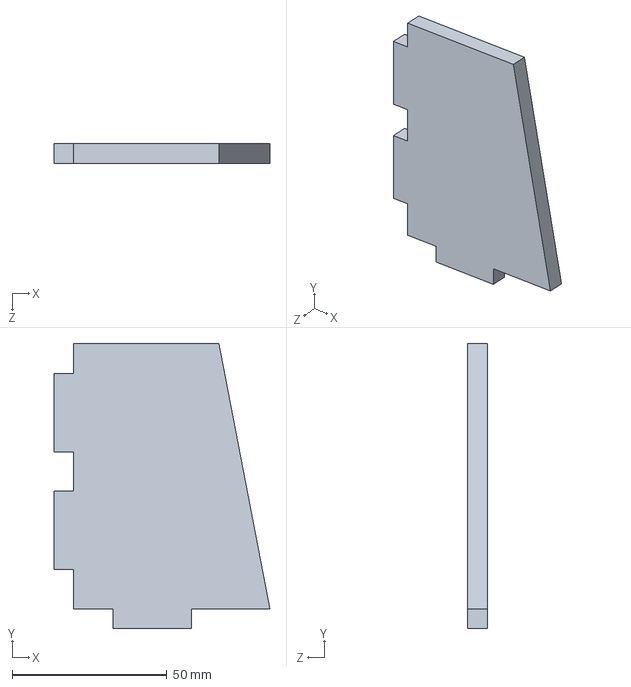
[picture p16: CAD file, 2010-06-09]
hardware/Rotation Table v3/motor mount support.SLDPRT
69.8 x 92.2 x 6.35 mm

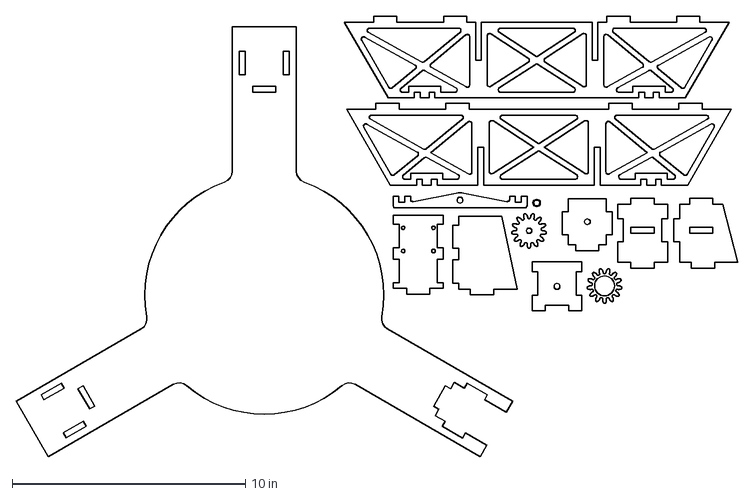
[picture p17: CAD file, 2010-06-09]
hardware/Rotation Table v3/parts1.DXF
31.0 x 18.9 in

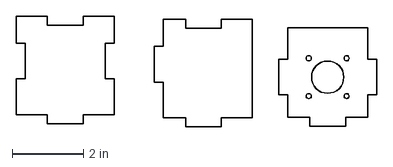
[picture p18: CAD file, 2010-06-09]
hardware/Rotation Table v3/spindle mount.DXF
10.1 x 3.09 in

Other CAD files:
hardware/Rotation Table v3/base truss 1.SLDPRT
hardware/Rotation Table v3/spindle mount lateral.SLDPRT
hardware/Rotation Table v3/bearing stand v2.SLDPRT
hardware/Rotation Table v3/spindle mount top.SLDPRT
hardware/Rotation Table v3/Drawing1.SLDDRW
hardware/Rotation Table v3/Drawing2.SLDDRW
hardware/Rotation Table v3/Table gear.SLDPRT
hardware/Rotation Table v3/base plate with spindle slots.DXF
hardware/Rotation Table v3/base platev2.DXF
hardware/Rotation Table v3/bearing spacer.SLDPRT
hardware/Rotation Table v3/pittmanservo.SLDPRT
hardware/Rotation Table v3/support Pinion.SLDPRT
hardware/Rotation Table v3/support pinion mount center.SLDPRT
hardware/Rotation Table v3/support pinion mount front.SLDPRT
hardware/Rotation Table v3/support pinion mount lateral.SLDPRT
hardware/Rotation Table v3/support pinion mount top.SLDPRT
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

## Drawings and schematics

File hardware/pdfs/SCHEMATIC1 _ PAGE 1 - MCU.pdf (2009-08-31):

0 0

0

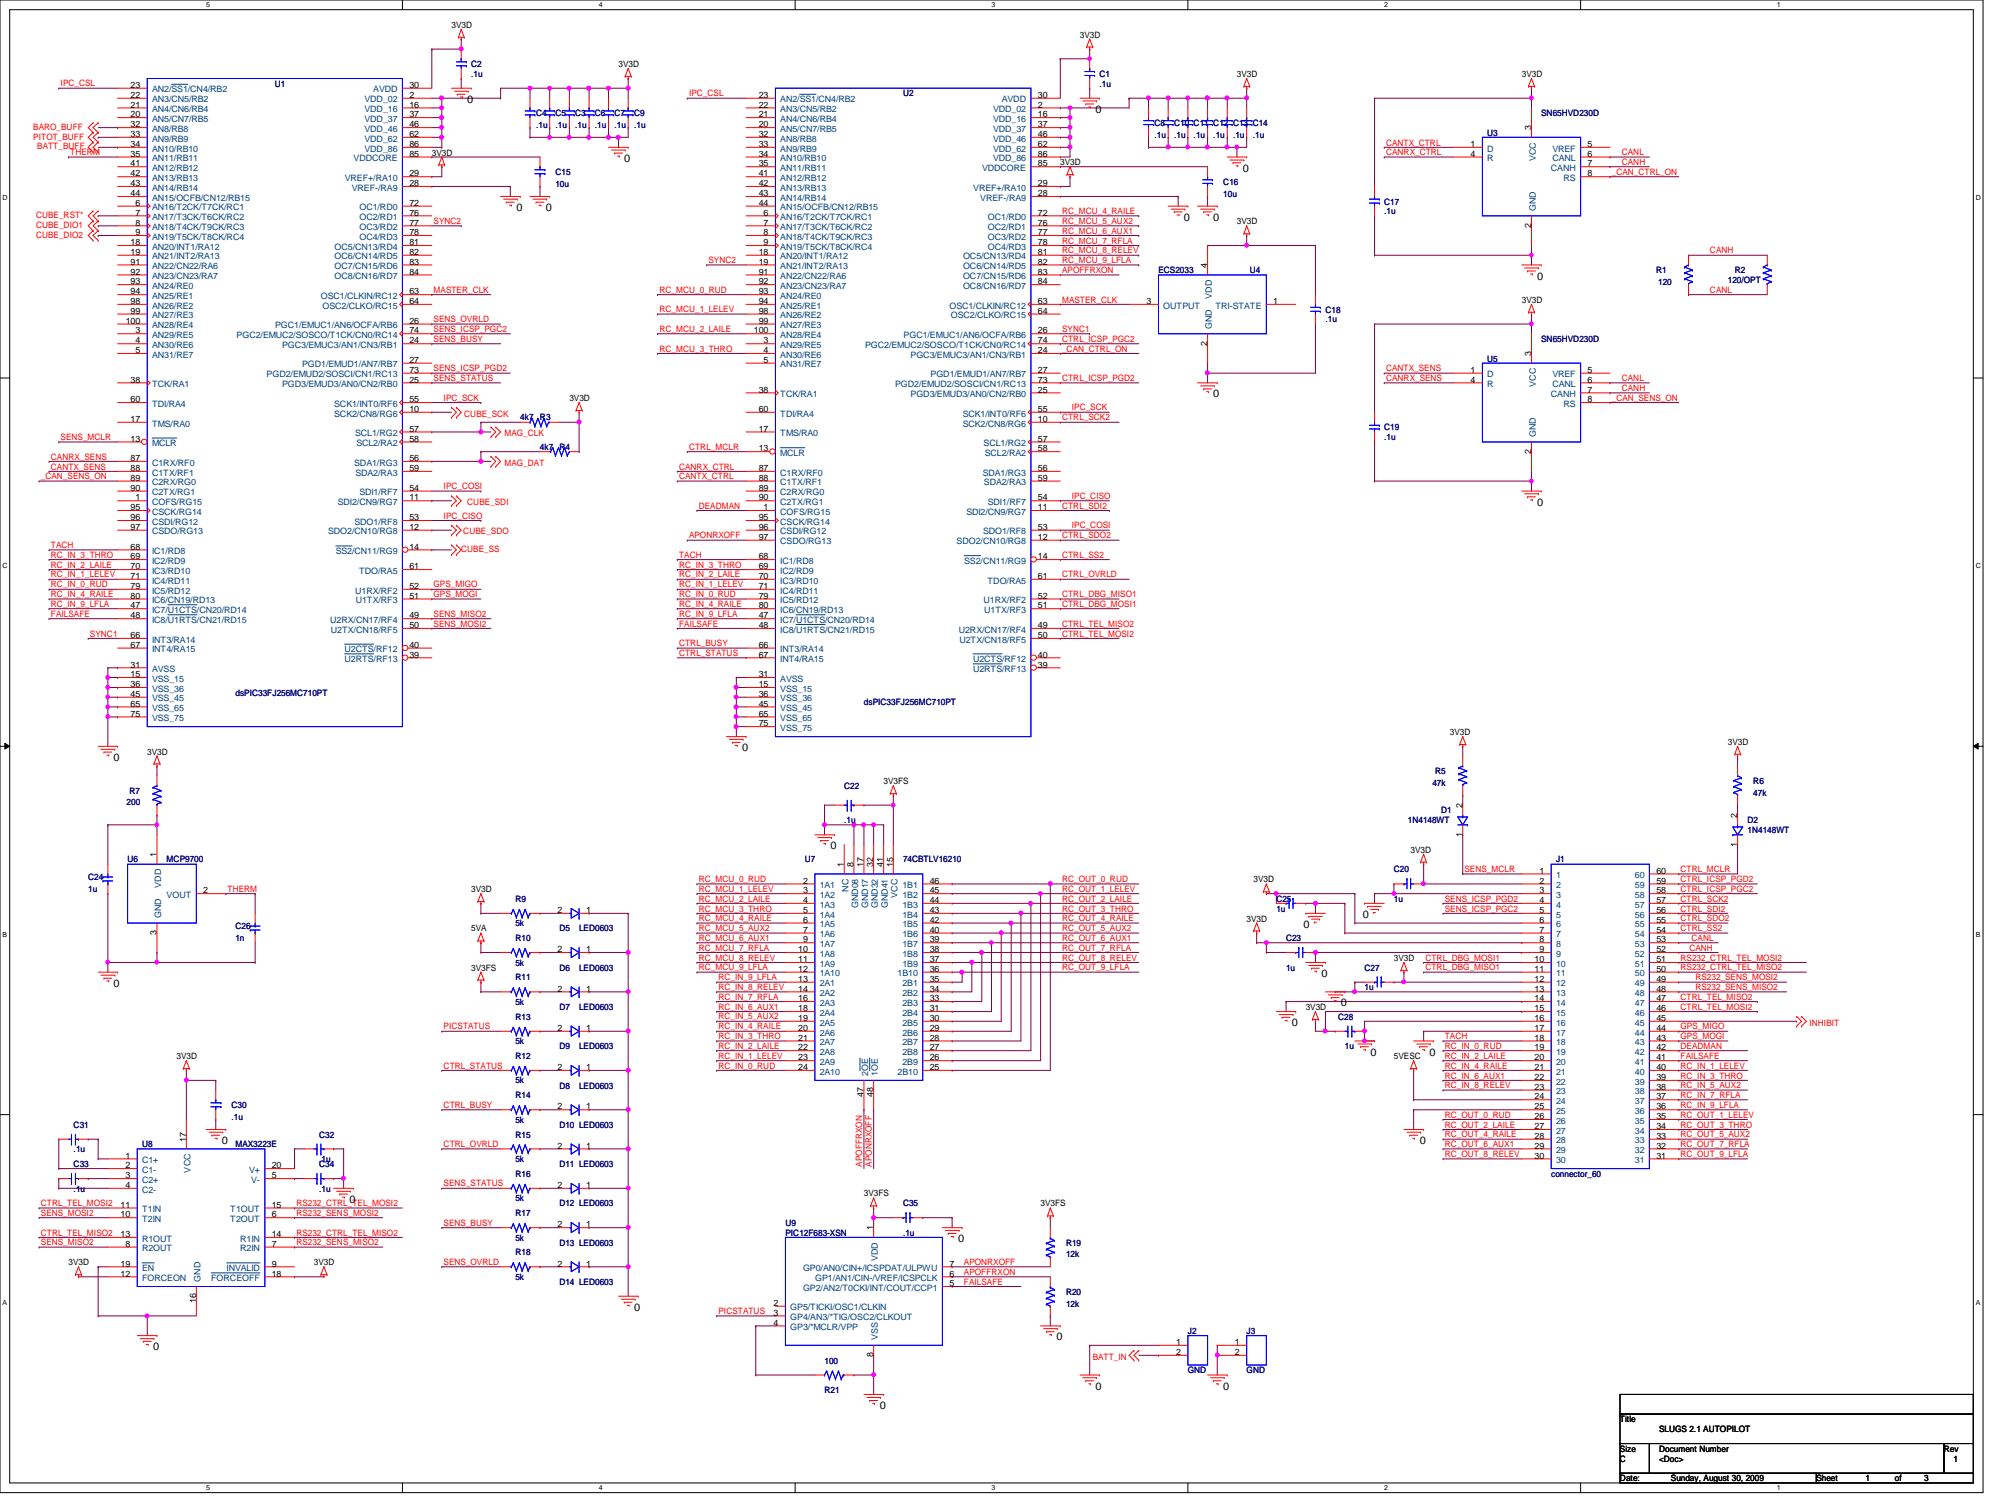
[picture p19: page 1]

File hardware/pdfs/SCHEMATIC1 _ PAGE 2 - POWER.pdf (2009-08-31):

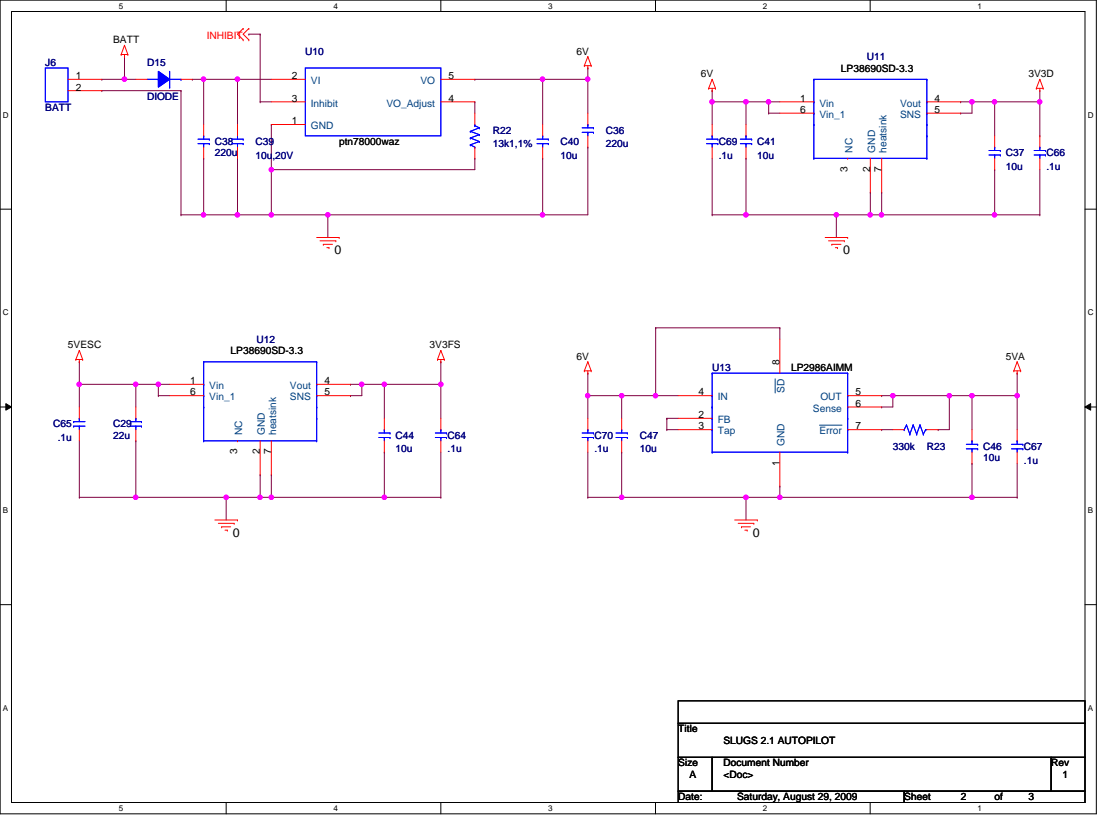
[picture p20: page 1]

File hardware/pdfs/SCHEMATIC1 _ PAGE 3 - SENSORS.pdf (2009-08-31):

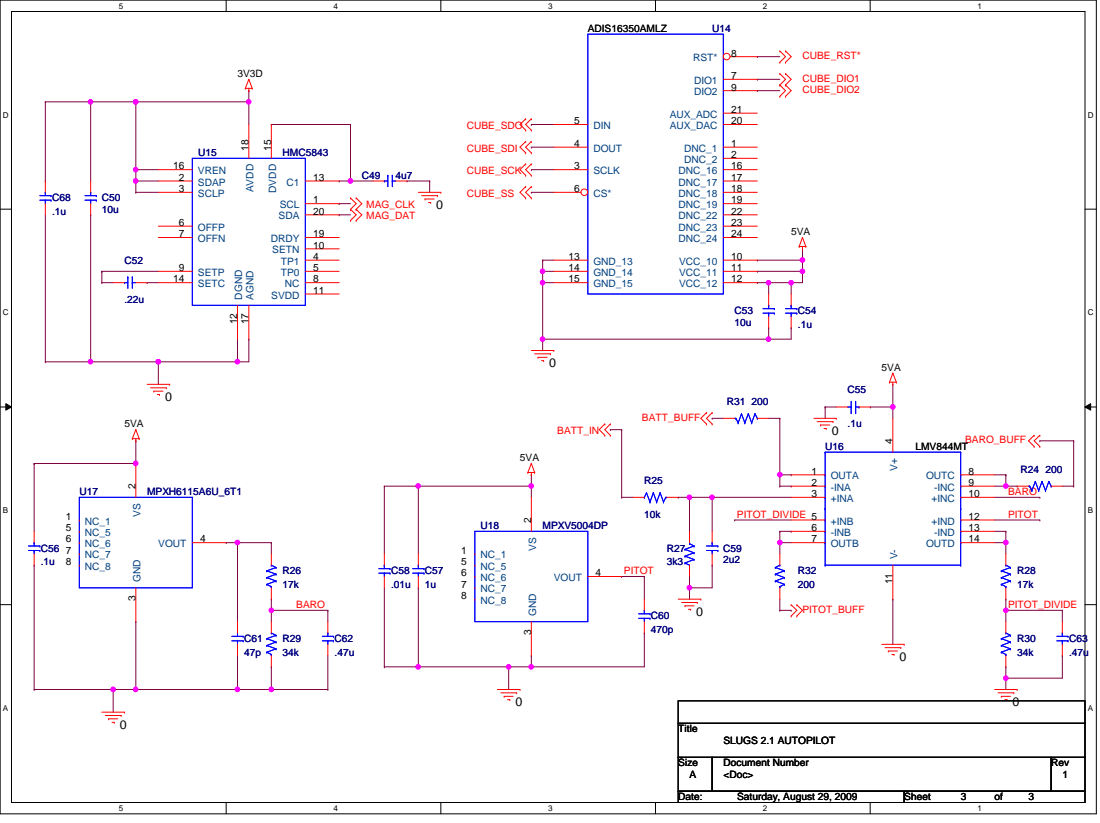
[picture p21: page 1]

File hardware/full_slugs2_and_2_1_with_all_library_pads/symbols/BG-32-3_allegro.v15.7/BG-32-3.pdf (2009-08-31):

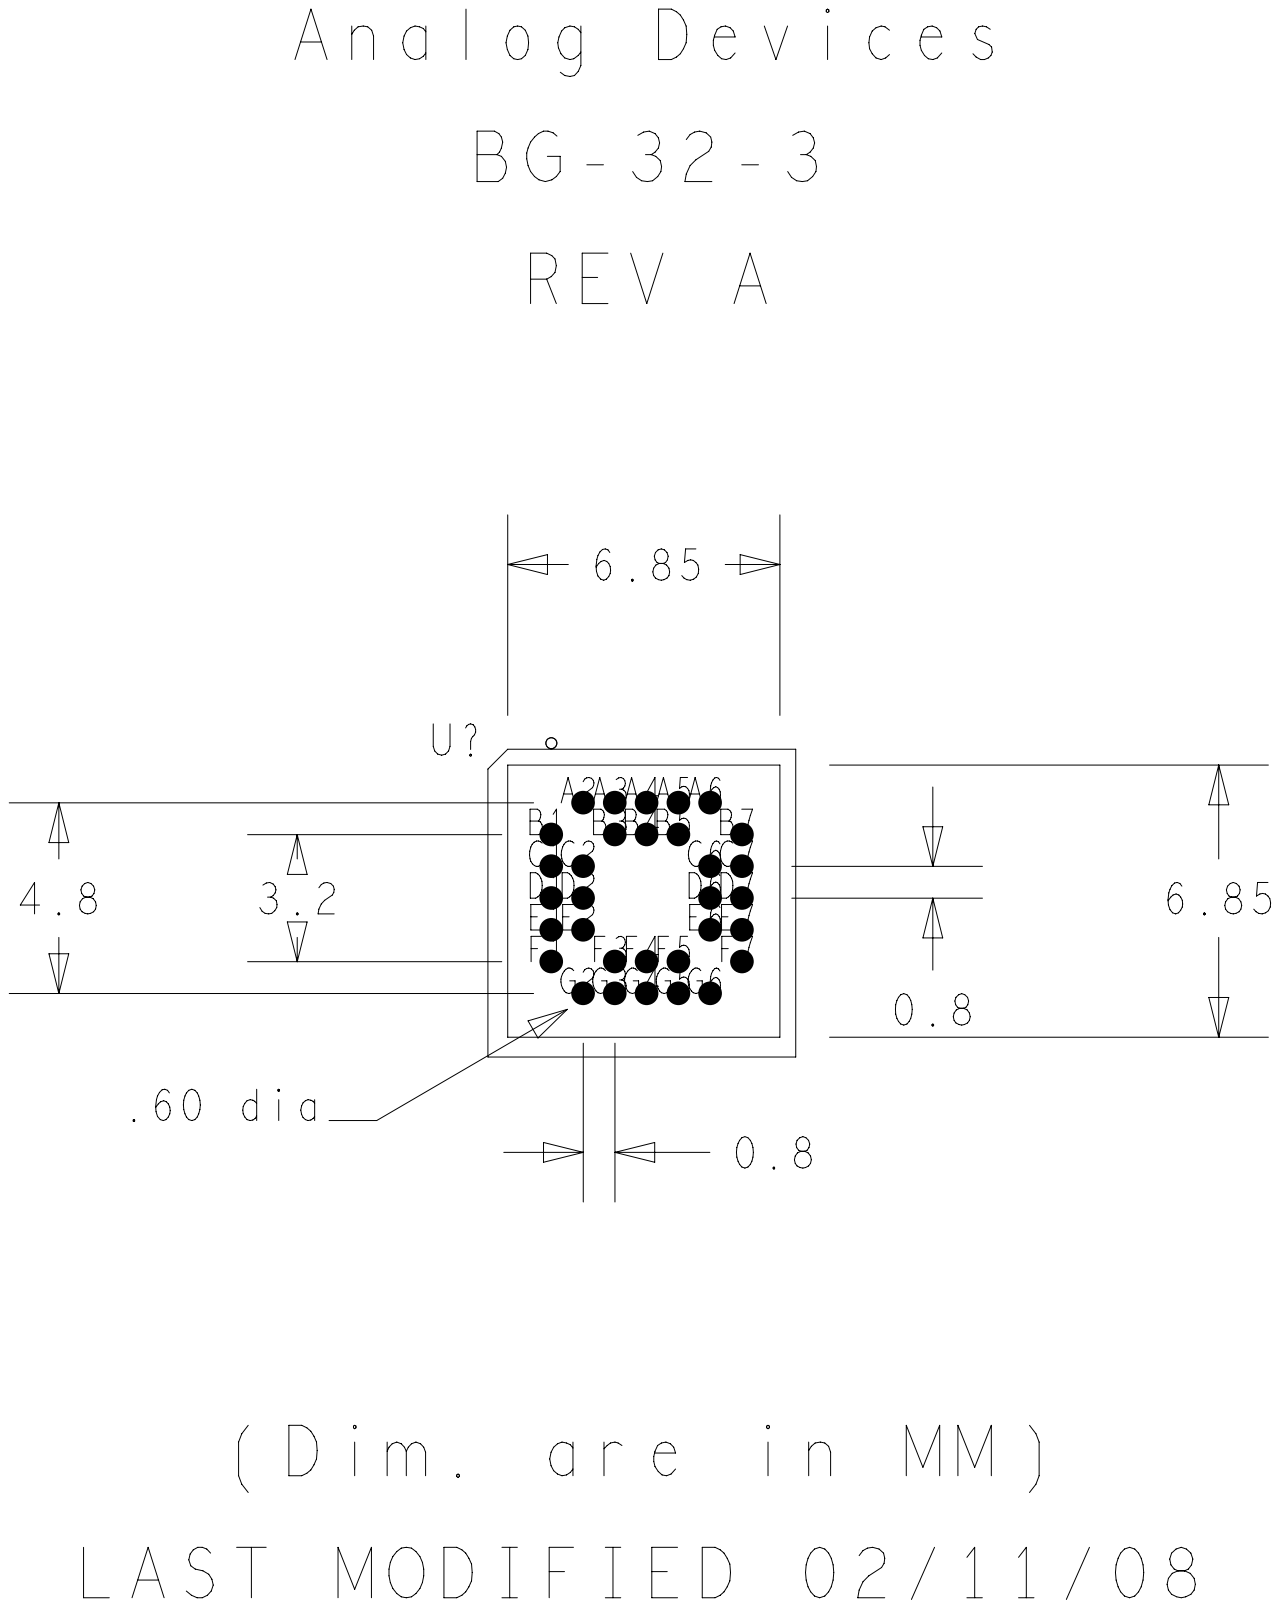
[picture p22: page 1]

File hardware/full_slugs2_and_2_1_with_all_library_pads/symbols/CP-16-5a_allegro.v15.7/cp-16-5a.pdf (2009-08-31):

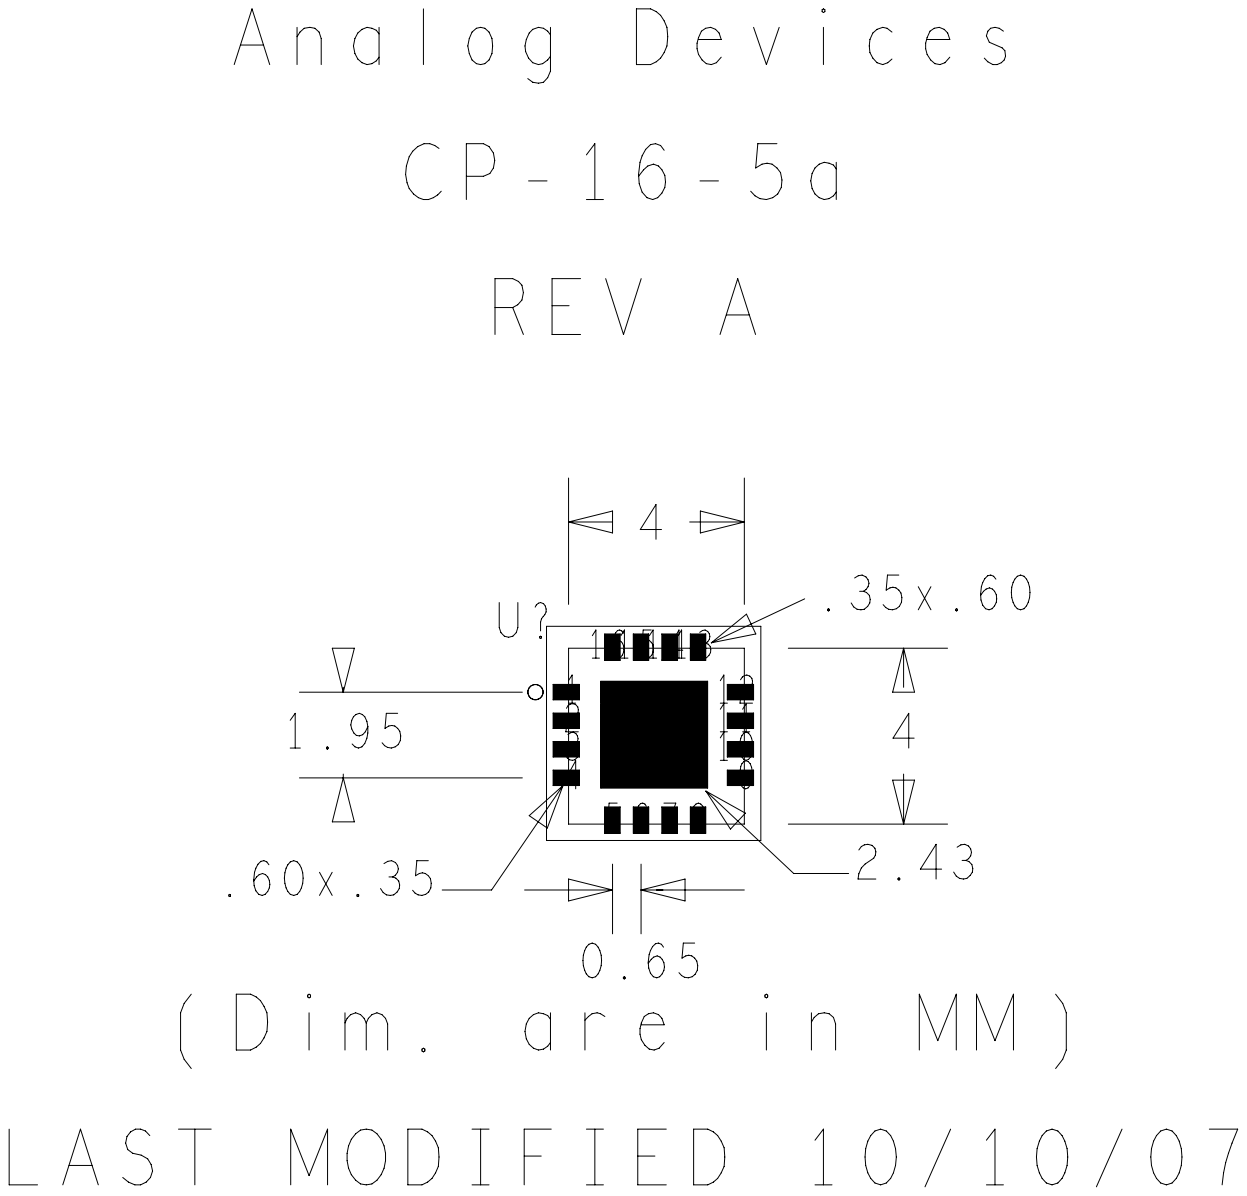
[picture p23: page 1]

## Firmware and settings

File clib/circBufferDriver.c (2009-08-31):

/*
The MIT License

Copyright (c) 2009 UCSC Autonomous Systems Lab

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
*/

#include <stdio.h>
#include <stdarg.h>
#include <string.h>
#include "circBuffer.h"
// #include "gpsSplit.h"
 // #include "apDefinitions.h"
// #include "gpsParse.h"
#include "gps.h"

unsigned char quickSort(unsigned short *arr, char elements) {

  #define  MAX_LEVELS  6

  unsigned short  piv, beg[MAX_LEVELS], end[MAX_LEVELS], i=0, L, R ;

  beg[0]=0; end[0]=elements;
  while (i>=0) {
    L=beg[i]; R=end[i]-1;
    if (L<R) {
      piv=arr[L]; if (i==MAX_LEVELS-1) return 0;
      while (L<R) {
        while (arr[R]>=piv && L<R) {
        	R--; 
        }
        if (L<R){ 
        	arr[L++]=arr[R];
        }
        while (arr[L]<=piv && L<R) {
        	L++;
        } 
        if (L<R) {
        	arr[R--]=arr[L];
      	}   
      }
      arr[L]=piv; beg[i+1]=L+1; end[i+1]=end[i]; end[i++]=L; 
    } else {
      i--;     
    }
  }
  return 1; 
}

int main(int argc, char* argv[])
{
	unsigned short myArray[] ={1456, 7856, 1450, 1423, 1423 }
	char i;
	
	quickSort(&myArray[0], 5)
	
	for( i = 0; i < 5; i += 1 )
	{
		printf("%d ", myArray[i]);
	}
	
  /*char str[] ="- This,a,,,,,sample,string.";
  char * pch;
	char count = 0;
	char str2[] = "This,is,a,,,,,,,sample,string";
	char token[TOKEN_SIZE];
	
  printf ("Splitting string \"%s\" into tokens using strtok:\n",str);
  pch = strtok (str,",");
  while (pch != NULL)
  {
    printf ("%d\t%s\n",count++,pch);
    pch = strtok (NULL, ",");
  }


  // char * pch;
  printf ("Looking for the ',' character in \"%s\"... using strchr \n",str2);
  pch=strchr(str2,',');
  while (pch!=NULL)
  {
    printf ("found at %d\n",pch-str2+1);
    pch=strchr(pch+1,',');
  }

  printf ("Looking for the ',' character in \"%s\"... using myTokenizer \n",str2);
  myTokenizer(str2,',', token);
  printf ("found token %s\n",token);
	while (!myTokenizer(NULL, ',', token))
  {
    printf ("found token %s\n",token);
  }
	printf ("found token %s\n",token);
	*/
	
	// unsigned char msg1 [] = "@$GPRMC,040302.663,A,3939.7,N,10506.6,W,5.27,358.86,200804,,*1A\r\n\0";
	// 	unsigned char msg2 [] = "N$GPGGA,213924.000,4221.1129,N,07102.9146,W,1,04,3.9,129.7,M,-33.7,M,,0000*68\r\n";
	// 	unsigned char msg3 [] = "&$GPGGA,213922.000,4221.1129,N,07102.91";
	// 	unsigned char msg4 [] = "(46,W,1,04,3.9,129.7,M,-33.7,M,,0000*6E\r\n";
	// 	
	// 	char i;
	// 	
	// 	float gpsData[5] = {0.0, 0.0, 0.0, 0.0, 0.0};
	// 	gpsInit();
	// 	
	// 	for(i=0; i<strlen(msg1); i++){
	// 		writeBack(uartBuffer, (unsigned char)msg1[i]);
	// 	}
	// 	for(i=0; i<strlen(msg2); i++){
	// 		writeBack(uartBuffer, (unsigned char)msg2[i]);
	// 	}
	// 	for(i=0; i<strlen(msg3); i++){
	// 		writeBack(uartBuffer, (unsigned char)msg3[i]);
	// 	}
	// 	
	// 	printf("%c\n\r", peak(uartBuffer));
	// 	
	// 	getGpsMainData(gpsData);
	// 	
	// 	printf("%f\t%f\t%f\t%f\t%f\n\r", gpsData[0], gpsData[1], gpsData[2], gpsData[3], gpsData[4]);
	// 
	// 	printf("%d\n\r", getLength(uartBuffer));
	
   return(0);
}
	
	
 /*  char i;
 
	
	unsigned char msg1 [] = "@$GPRMC,040302.663,A,3939.7,N,10506.6,W,5.27,358.86,200804,,*1A\r\n";
	unsigned char msg2 [] = "N$GPGGA,213924.000,4221.1129,N,07102.9146,W,1,04,3.9,129.7,M,-33.7,M,,0000*68\r\n";
	unsigned char msg3 [] = "&$GPGGA,213922.000,4221.1129,N,07102.91";
	unsigned char msg4 [] = "(46,W,1,04,3.9,129.7,M,-33.7,M,,0000*6E\r\n";
	
	unsigned char outBuffer [128] ={0}, parsedData[128]={0};
	
	gpsInit();
	
	printf("Message 1\n");
	gpsSeparate(msg2, outBuffer);	
		printf("\n");
		printf(outBuffer);
		printf("\nValid: %d Type:%d", outBuffer[MSIZE-1], outBuffer[0]);
		printf("\n");
		printf(msg2);
	
	gpsParse(outBuffer, parsedData);
	
	for(i=0;i<6;i++){
		printf("%d ", parsedData[i]);
	}
	
	tFloatToChar flCh;
	tIntToChar inCh;
	
	flCh.chData[0] = parsedData[6];
	flCh.chData[1] = parsedData[7];
	flCh.chData[2] = parsedData[8];
	flCh.chData[3] = parsedData[9];
	printf("%f ", flCh.flData);
	
	flCh.chData[0] = parsedData[10];
	flCh.chData[1] = parsedData[11];
	flCh.chData[2] = parsedData[12];
	flCh.chData[3] = parsedData[13];
	printf("%f ", flCh.flData);

	flCh.chData[0] = parsedData[14];
	flCh.chData[1] = parsedData[15];
	flCh.chData[2] = parsedData[16];
	flCh.chData[3] = parsedData[17];
	printf("%f ", flCh.flData);
	
	inCh.chData[0] = parsedData[18];
	inCh.chData[1] = parsedData[19];
	printf("%d ", inCh.inData);

	inCh.chData[0] = parsedData[20];
	inCh.chData[1] = parsedData[21];
	printf("%d ", inCh.inData);
	
	inCh.chData[0] = parsedData[22];
	inCh.chData[1] = parsedData[23];
	printf("%d ", inCh.inData);
	
	for(i=24;i<26;i++){
		printf("%d ", parsedData[i]);
	}
	
	printf("\n");
	
	unsigned char thischr [] = "$PMTK251,19200*22\r\n";
	printf("Baud Rate %d", getChecksum(thischr, 17));
	
	unsigned char thischr2 [] = "$PMTK300,200,0,0,0,0*2F\r\n";
	printf("Frequency %d", getChecksum(thischr2, 23));
	
	unsigned char thischr3 [] = "$PMTK314,0,1,0,1,0,0,0,0,0,0,0,0,0,0,0,0,0,0,0*28\r\n";
	printf("Sentences %d", getChecksum(thischr3, 49));
				
	/*printf("Message 2\n");
	gpsSeparate(msg2, outBuffer);	
		printf("\n");
		printf(outBuffer);
		printf("\nValid: %d Type:%d", outBuffer[MSIZE-1], outBuffer[0]);
		printf("\n");
		printf(msg2);
	


	printf("First Call to GPS Separate\n");
	gpsSeparate(msg3, outBuffer);	
	printf("============================\n");
	
	printf("Second Call to GPS Separate\n");	
	gpsSeparate(msg4, outBuffer);	
	printf("============================\n");
	
	printf(outBuffer);
	printf("\nValid: %d Type:%d", outBuffer[MSIZE-1], outBuffer[0]);
	printf("\n");
	printf(msg3);
	printf(msg4);

	printf("============================\n");
	printf("============================\n");
	printf("============================\n");
	printf("============================\n");
	printf("Char: %d, Short: %d, Int: %d, Float: %d, Long:%d", sizeof(char), sizeof(short), sizeof(int), sizeof(float), sizeof(long));
	printf("\n");	
	*/

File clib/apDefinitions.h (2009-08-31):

/*
The MIT License

Copyright (c) 2009 UCSC Autonomous Systems Lab

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
*/

	/* ==================================================
This is the definition file for the the UCSC AP code
it creates all the common defines, unions, enumerations
and data types.

 Code by: Mariano I. Lizarraga
 First Revision: Aug 18 2008 @ 17:42
 ====================================================*/
#ifndef _APDEFINITIONS_H_
#define _APDEFINITIONS_H_

#ifdef __cplusplus
       extern "C"{
#endif

// =========== Global Definitions ==========

// Circular Buffer Size
// ===================
#ifdef __cplusplus
       #define BSIZE			1024
#else
       #define BSIZE			512
#endif

// GPS Checksum Messages
// =====================
#define GGACS			86
#define RMCCS			75

// GPS Header IDs
// ==============
#define GGAID			1
#define RMCID			2
#define UNKID			254

// GPS Circular Buffers
// ====================
#define MSIZE			150
#define CSIZE			26 //[newBytes payload remaingBytes]  (comms buffer out of readGPS)

// Data Logger Values
// ================
#define LOGSEND					8
#define MAXSEND					103
#define MAXLOGSEND				56

#ifdef __cplusplus
       #define MAXLOGLEN		500
#else
       #define MAXLOGLEN		99
#endif

// Define log raw data at 100 hz. Comment out to have
// XYZ data come at 100 Hz instead. COMMENT not Change to 0 (using #ifdef)
//#define LOGRAW100	1

// Define diagnostic data at 100 hz. Comment out to have
// XYZ data come at 100 Hz instead. COMMENT not Change to 0 (using #ifdef)
#define DIAG100		1

// Message Protocol Lengths and IDs
// ================================

// SENSOR MCU
// ==========
#define GPS_START 		0
#define GPSMSG_ID		1
#define GPSMSG_LEN		27 

#define LOAD_START		27
#define LOADMSG_ID		2
#define LOADMSG_LEN		4

#define RAW_START 		31
#define RAWMSG_ID		3
#define RAWMSG_LEN		26

#define ATT_START		49
#define ATTMSG_ID		4
#define ATTMSG_LEN		26

#define XYZ_START		75
#define XYZMSG_ID		11
#define XYZMSG_LEN		24

#define DYN_START		99
#define DYNMSG_ID		5
#define DYNMSG_LEN		10

#define BIA_START		109
#define BIAMSG_ID		6
#define BIAMSG_LEN		24

#define DIA_START		133
#define DIAMSG_ID		7
#define DIAMSG_LEN		18

#define HIL_START		151

#define PIL_START		152
#define PILMSG_ID		9
#define PILMSG_LEN		10

#define SENMSG_ID		25
#define SENMSG_LEN		24

#define LOGMSG_ID		26
#define LOGMSG_LEN	24

// CONTROL MCU
// ===========
#define AKNMSG_ID		105
#define AKNMSG_LEN		6

#define PWMMSG_ID		100
#define PWMMSG_LEN		20 

#define CALMSG_ID		102
#define CALMSG_LEN		17

#define APSMSG_ID		101
#define APSMSG_LEN		20

#define NAVMSG_ID		120
#define	NAVMSG_LEN	30


// GROUND STATION
// ==============
// NOTE: for HIL simulator the GS uses the same IDs for the 
// simulated sensor readings, i.e. GPS, Raw, Air Data, etc. Than
// for the actual readings.

#define FILMSG_ID		205
#define FILMSG_LEN		1

#define PIDMSG_ID		202
#define PIDMSG_LEN		13

#define QUEMSG_ID		204
#define QUEMSG_LEN		10

#define WPSMSG_ID		201
#define WPSMSG_LEN		16

#define COMMSG_ID		206
#define COMMSG_LEN		10

#define CHSMSG_ID		207
#define CHSMSG_LEN		9


// Identifier values for messages that have a type ID
// ==================================================

// Calibration and Query type IDs
#define PIDTYPE_ID		1
#define WPSTYPE_ID		2
#define PASTYPE_ID		3
#define COMTYPE_ID		4

// Control Types
#define CTRL_TYPE_MANUAL	1		// Pilot in full control of aircraft
#define CTRL_TYPE_AP_COMM	2		// Low level commands: airspeed, height and turnrate
#define CTRL_TYPE_AP_WP		3		// Waypoint following
#define CTRL_TYPE_PASS		4		// Passthrough the commands from the pilot console
#define CTRL_TYPE_SEL_PIL	5		// Pass some from the pilot and some from the AP
#define CTRL_TYPE_SEL_AP	6

#define PIL_FAILSAFE		6000	// IC direct reading from the pilot console when failsafe is
									// is turned ON i.e. the pilot is in control. 

// Commands to AP ids
#define COMM_TYPE_HEIGHT	1
#define	COMM_TYPE_TURNRATE	2
#define	COMM_TYPE_AIRSPEED	3
#define COMM_TYPE_GOTO_WP	4



// ERROR MESSAGES
// ==============

// PID EEPROM Error Messages
#define PIDEEP_WRITE_FAIL	11
#define PIDEEP_PAGE_EXP		12
#define PIDEEP_MEMORY_CORR	13

// WP EEPROM Error Messages
#define WPSEEP_WRITE_FAIL	21
#define WPSEEP_PAGE_EXP		22
#define WPSEEP_MEMORY_CORR	23

// EEPROM Emulation Address Offsets
// ================================
#define PID_OFFSET		0
#define WPS_OFFSET		60

// Communication Protocol Merging Offsets
// ======================================
#define GSMSG_IDX		99
#define AKMSG_IDX		202


// Standard characters used in the parsing of messages
// ===================================================
#define DOLLAR			36
#define STAR			42
#define CR				13
#define LF				10
#define AT				64

// Interprocessor Communication
// ============================
#define BEGINSPI		0xFFFF
#define ENDSPI			0xBEEF
#define SPIBUFSIZE		46
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

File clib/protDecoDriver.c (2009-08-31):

/*
The MIT License

Copyright (c) 2009 UCSC Autonomous Systems Lab

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
*/

#include <stdio.h>
#include <stdarg.h>
#include <string.h>
#include <stdlib.h>
#include "protDecoder.h"
#include "apDefinitions.h"
#include "gpsSplit.h"
#include "circBuffer.h"

	unsigned char msg1 [] = {0x24, 0x40, 0x01, 0x1b, 0x00, 0x00, 0x00, 0x00,
    0x00, 0x00, 0x00, 0x00, 0x00, 0x00, 0x00, 0x00, 0x00, 0x00, 0x00, 0x00,
    0x00, 0x00, 0x00, 0x00, 0x00, 0x00, 0x00, 0x00, 0x00, 0x00, 0x00, 0x2a,
    0x40, 0x5a};

    unsigned char msg2[] = {0x24, 0x40, 0x02, 0x04, 0x00, 0x01, 0x02, 0x03,
    0x2a, 0x40, 0x46};

    unsigned char msg3[] = {0x24, 0x40, 0x03, 0x12, 0x44, 0x07, 0xf2, 0x07,
    0xf6, 0x07, 0xdb, 0x07, 0xdd, 0x07, 0x5f, 0x09, 0xf9, 0x0f, 0xf9, 0x0f,
    0xf9, 0x0f, 0x2a, 0x40, 0xb0};

    unsigned char msg4[] = {0x24, 0x40, 0x04, 0x18, 0x24, 0x60, 0xc5, 0x3d,
    0x6d, 0x95, 0x83, 0x3d, 0x6d, 0x95, 0x03, 0x3e, 0x24, 0x60, 0xc5, 0x3d,
    0x6d, 0x95, 0x83, 0x3d, 0x6d, 0x95, 0x03, 0x3e, 0x2a, 0x40, 0x5c};

    unsigned char msg11[]= {0x24, 0x40, 0x0b, 0x0c, 0x24, 0x60, 0xc5, 0x3d,
    0x6d, 0x95, 0x83, 0x3d, 0x6d, 0x95, 0x03, 0x3e, 0x2a, 0x40, 0x3d};


    unsigned char retV[16];

    struct CircBuffer com2Buffer;
    CBRef logBuffer;

void assembleMsg(unsigned char* rawData , unsigned char size, unsigned char type, unsigned char* protMsg ){
	unsigned char i;
	// start the header
	*(protMsg+0) = DOLLAR;
	*(protMsg+1) = AT;
	*(protMsg+2) = type;
	*(protMsg+3) = size;
	for( i = 0; i < size; i += 1 )
	{
		*(protMsg+i+4) = *(rawData +i);
	}
	*(protMsg+size+4) = STAR;
	*(protMsg+size+5) = AT;
	*(protMsg+size+6) = getChecksum(protMsg, (size+5));	
}

void logData (unsigned char* rawData, unsigned char* data4SPI){
	// sample period variable
	static unsigned char samplePeriod = 0;
	unsigned char tmpBuf [MAXLOGLEN];

	// temp var to store the assembled message
	unsigned char i;
	unsigned char len2SPI=0;
	unsigned char bufLen = 0;

	memset(tmpBuf, 0, sizeof(tmpBuf));
    	
	switch (samplePeriod){
		case 2:
			// assemble the CPU load data for protocol sending	
			assembleMsg(&rawData[LOAD_START], LOADMSG_LEN, LOADMSG_ID, tmpBuf);
			// set the total data out for SPI
			len2SPI = LOADMSG_LEN+7; 			
			// add it to the circular buffer and SPI queue
			for( i = 0; i < LOADMSG_LEN+7; i += 1 ){
				writeBack(logBuffer,tmpBuf[i]);
				data4SPI[i+1] = tmpBuf[i];
			}

			break;
		case 3:			
			// assemble the Raw Sensor data for protocol sending	
			assembleMsg(&rawData[RAW_START], RAWMSG_LEN, RAWMSG_ID, tmpBuf);
			// set the total data out for SPI			
			len2SPI = RAWMSG_LEN+7; 			
			// add it to the circular buffer and SPI queue
			for( i = 0; i < RAWMSG_LEN+7; i += 1 ){
				writeBack(logBuffer,tmpBuf[i]);
				data4SPI[i+1] = tmpBuf[i];
			}
		
			break;
		case 1:
			// assemble the GPS data for protocol sending
			assembleMsg(&rawData[GPS_START], GPSMSG_LEN, GPSMSG_ID, tmpBuf);
			// set the total data out for SPI
			len2SPI = GPSMSG_LEN+7; 
			// add it to the circular buffer and SPI queue
			for( i = 0; i < GPSMSG_LEN+7; i += 1 ){
				writeBack(logBuffer,tmpBuf[i]);
				data4SPI[i+1] = tmpBuf[i];
			}					
			break;
		default:
			data4SPI[0] = 0;
			break;
	}

	memset(tmpBuf, 0, sizeof(tmpBuf));

	// Attitude data. Gets included every sample time
	// ==============================================
	
	// assemble the Attitude data for protocol sending
	assembleMsg(&rawData[ATT_START], ATTMSG_LEN, ATTMSG_ID, tmpBuf);
	
	// add it to the circular buffer and SPI queue
	for( i = 0; i < ATTMSG_LEN+7; i += 1 ){
		writeBack(logBuffer,tmpBuf[i]);
		data4SPI[i+1+len2SPI] = tmpBuf[i];
	}					
	
	// increment the data counter for SPI
	len2SPI += ATTMSG_LEN+7; 
	
	memset(tmpBuf, 0, sizeof(tmpBuf));
    
	// XYZ data. Gets included every sample time
	// ==============================================
	
	// assemble the XYZ data for protocol sending
	assembleMsg(&rawData[XYZ_START], XYZMSG_LEN, XYZMSG_ID, tmpBuf);
	// add it to the circular buffer and SPI queue
	for( i = 0; i < XYZMSG_LEN+7; i += 1 ){
		writeBack(logBuffer,tmpBuf[i]);
		data4SPI[i+1+len2SPI] = tmpBuf[i];
	}
	
    // set the total data out for SPI
	data4SPI[0] = len2SPI + XYZMSG_LEN+7; 

	
	// increment/overflow the samplePeriod counter
	samplePeriod = (samplePeriod >= 4)? 0: samplePeriod + 1;
	
	// get the Length of the logBuffer
	bufLen = getLength(logBuffer);
	
   /*	// if the interrupt catched up with the circularBuffer
	//  then turn on the DMA
	if(!(DMA0CONbits.CHEN) && bufLen> 0){
		// Configure the bytes to send
		DMA0CNT =  bufLen<= (MAXSEND-1)? bufLen-1: MAXSEND-1;
		// copy the buffer to the DMA channel outgoing buffer
		copyBufferToDMA((unsigned char) DMA0CNT);
		// Enable the DMA
		DMA0CONbits.CHEN = 1;
		// Init the transmission
		DMA0REQbits.FORCE = 1;
	}

    */
}



int main (int argc, char const* argv[])
{
    FILE *file;
	unsigned char *buffer;
	unsigned long fileLen;
    unsigned long i;

    unsigned char mychk;
    unsigned char myRawData[97];
    unsigned char myData4SPI[97];
    unsigned char myToLog[97];

    logBuffer = (struct CircBuffer* )&com2Buffer;
	newCircBuffer(logBuffer);

    memset(myRawData,0,sizeof(myRawData));
    memset(myData4SPI,0,sizeof(myData4SPI));

    // create the raw stream
    //====================
    for(i=0; i< GPSMSG_LEN; i+=1){
        myRawData[i] = msg1[4+i];
    }

    for(i=GPSMSG_LEN; i< (GPSMSG_LEN + LOADMSG_LEN); i+=1){
        myRawData[i] = msg2[4+i-GPSMSG_LEN];
    }

    for(i=(GPSMSG_LEN + LOADMSG_LEN); i< (GPSMSG_LEN + LOADMSG_LEN + RAWMSG_LEN); i+=1){
        myRawData[i] = msg3[4+i - (GPSMSG_LEN + LOADMSG_LEN)];
    }

    for(i=(GPSMSG_LEN + LOADMSG_LEN + RAWMSG_LEN); i< (GPSMSG_LEN + LOADMSG_LEN + RAWMSG_LEN+ATTMSG_LEN); i+=1){
        myRawData[i] = msg4[4+i-(GPSMSG_LEN + LOADMSG_LEN + RAWMSG_LEN)];
    }


    for(i=(GPSMSG_LEN + LOADMSG_LEN + RAWMSG_LEN+ATTMSG_LEN); i< (GPSMSG_LEN + LOADMSG_LEN + RAWMSG_LEN+ATTMSG_LEN + XYZMSG_LEN); i+=1){
        myRawData[i] = msg11[4+i-(GPSMSG_LEN + LOADMSG_LEN + RAWMSG_LEN+ATTMSG_LEN)];
    }

    //====================

    /*for (i=0;i<10 ;i+=1)
    {
      logData(myRawData,myData4SPI);
      myData4SPI;
      memset(myData4SPI,0,sizeof(myData4SPI));
    }*/

    
	//Open file
	file = fopen("prot.bin", "rb");
	if (!file)
	{
		fprintf(stderr, "Unable to open file");
		return 0;
	}
	
	//Get file length
	fseek(file, 0, SEEK_END);
	fileLen=ftell(file);
	fseek(file, 0, SEEK_SET);

	//Allocate memory
	buffer=(unsigned char *)malloc(fileLen+1);
	if (!buffer)
	{
		fprintf(stderr, "Memory error!");
                                fclose(file);
		return 0;
	}

        protParserInit();

	//Read file contents into buffer
        i = 0;
        while (i<fileLen-96){
	        fread(buffer, 96, 1, file);
            i+=96;
            protParseDecode(buffer, myToLog);
        }
        fclose(file);
	//Do what ever with buffer

	free(buffer);



	return 0;
}

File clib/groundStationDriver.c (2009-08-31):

/*
The MIT License

Copyright (c) 2009 UCSC Autonomous Systems Lab

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
*/

#include "groundStationDriver.h"

struct CircBuffer com1BufferIn;
CBRef uartBufferIn;

struct CircBuffer com1BufferOut;
CBRef uartBufferOut;

struct CircBuffer gsParseBuffer;
CBRef gsBuffer;

unsigned int BufferB[MAXSEND] __attribute__((space(dma))) = {0};

// UART, DMA and Buffer initialization
void uart1Init (void){
	// initialize the circular buffers
	uartBufferIn = (struct CircBuffer* )&com1BufferIn;
	newCircBuffer(uartBufferIn);

	uartBufferOut = (struct CircBuffer* )&com1BufferOut;
	newCircBuffer(uartBufferOut);
	
	gsBuffer = (struct CircBuffer* )&gsParseBuffer;
	newCircBuffer(gsBuffer);
	
	// DMA1REQ Register
	// ================
	//DMA1REQ = 0x000C;
	// FIXME: Remove for UART 1 to work
	DMA1REQ = 0x001F;
	
	// DMA1PAD Register
	// ================
	//DMA1PAD = (volatile unsigned int) &U1TXREG;
	// FIXME: Remove for UART 1 to work
	DMA1PAD = (volatile unsigned int) &U2TXREG;
	
	// DMA1CON Register
	// ================
	DMA1CONbits.AMODE   = 0;        // Register Indirect with post-increment
	DMA1CONbits.MODE    = 1;        // One-shot, No Ping-Pong Mode	
	DMA1CONbits.DIR     = 1;        // Read from RAM and send to Periphereal
	DMA1CONbits.SIZE    = 0;        // Word Data Transfer

	// DMA1CNT Register
	// ==============
	DMA1CNT = LOGSEND-1;

	// DMA1STA Register
	// ================
	DMA1STA= __builtin_dmaoffset(BufferB);

	// Enable DMA1 TX interrupts
	IFS0bits.DMA1IF  = 0;			// Clear DMA Interrupt Flag
	IPC3bits.DMA1IP  = 6;			// interrupt priority to 6
	IEC0bits.DMA1IE  = 1;			// Enable DMA interrupt
	
	/*
	// Configure and open the port;
	// U1MODE Register
	// ==============
	U1MODEbits.UARTEN	= 0;		// Disable the port		
	U1MODEbits.USIDL 	= 0;		// Stop on idle
	U1MODEbits.IREN		= 0;		// No IR decoder
	U1MODEbits.RTSMD	= 0;		// Ready to send mode (irrelevant)
	U1MODEbits.UEN		= 0;		// Only RX and TX
	U1MODEbits.WAKE		= 1;		// Enable at startup
	U1MODEbits.LPBACK	= 0;		// Disable loopback
	U1MODEbits.ABAUD	= 0;		// Disable autobaud
	U1MODEbits.URXINV	= 0;		// Normal operation (high is idle)
	U1MODEbits.PDSEL	= 0;		// No parity 8 bit
	U1MODEbits.STSEL	= 0;		// 1 stop bit
	U1MODEbits.BRGH 	= 0;		// Low speed mode
	
	// U1STA Register
	// ==============
	U1STAbits.UTXISEL0	= 0;		// generate interrupt on every char
	U1STAbits.UTXISEL1	= 0;		// for the DMA	
	U1STAbits.URXISEL	= 0;		// RX interrupt when a char is in
	U1STAbits.OERR		= 0;		// clear overun error
	
	// U1BRG Register
	// ==============
	U1BRG = LOG_UBRG;				// Set the baud rate for 115,200
	
	// Initialize the Interrupt  
  	// ========================
	IPC2bits.U1RXIP   = 6;    		// Interrupt priority 6  
  	IFS0bits.U1RXIF   = 0;    		// Clear the interrupt flag
  	IEC0bits.U1RXIE   = 1;    		// Enable interrupts

	// Enable the port;
	U1MODEbits.UARTEN	= 1;		// Enable the port	
	U1STAbits.UTXEN		= 1;		// Enable TX
	
	IEC4bits.U1EIE 		= 0;
	*/
	//FIXME: Remove for UART 1 to work
		// Configure and open the port;
	// U2MODE Register
	// ==============
	U2MODEbits.UARTEN	= 0;		// Disable the port		
	U2MODEbits.USIDL 	= 0;		// Stop on idle
	U2MODEbits.IREN		= 0;		// No IR decoder
	U2MODEbits.RTSMD	= 0;		// Ready to send mode (irrelevant)
	U2MODEbits.UEN		= 0;		// Only RX and TX
	U2MODEbits.WAKE		= 1;		// Enable at startup
	U2MODEbits.LPBACK	= 0;		// Disable loopback
	U2MODEbits.ABAUD	= 0;		// Disable autobaud
	U2MODEbits.URXINV	= 0;		// Normal operation (high is idle)
	U2MODEbits.PDSEL	= 0;		// No parity 8 bit
	U2MODEbits.STSEL	= 0;		// 1 stop bit
	U2MODEbits.BRGH 	= 0;		// Low speed mode
	
	// U1STA Register
	// ==============
	U2STAbits.UTXISEL0	= 0;		// generate interrupt on every char
	U2STAbits.UTXISEL1	= 0;		// for the DMA	
	U2STAbits.URXISEL	= 0;		// RX interrupt when a char is in
	U2STAbits.OERR		= 0;		// clear overun error
	
	// U1BRG Register
	// ==============
	U2BRG = LOG_UBRG;				// Set the baud rate for 115,200
	
	// Initialize the Interrupt  
  	// ========================
	IPC7bits.U2RXIP   = 6;    		// Interrupt priority 6  
  	IFS1bits.U2RXIF   = 0;    		// Clear the interrupt flag
  	IEC1bits.U2RXIE   = 1;    		// Enable interrupts

	// Enable the port;
	U2MODEbits.UARTEN	= 1;		// Enable the port	
	U2STAbits.UTXEN		= 1;		// Enable TX
	
	IEC4bits.U2EIE 		= 0;

	
}

void controlMCUInit(void){
	unsigned char eepInitMsg = 0;
	
	// Initialize the SPI Port for IPC
	spiSlaveInit();
	
	// initialize the Protocol Parser and Decoder
	protParserInit();
	
	// Initialize the UART1 port for Telemetry
	uart1Init();
	
	// Initialize EEPROM emulator
	EEPInit();
	
	// Load Data from EEPROM if the initialization worked
	if (aknControlData.pidCal==0){
	   loadEEPData();
	}
	
	// Control MCU boot procedures
	#ifdef _IN_PC_
		//
	#else
		aknControlData.reboot = 1;		
	#endif
	
}

void EEPInit(void){
	unsigned char eepInitMsg = 0;
	
	// Initialize the EEPROM emulation and read the PID Data
	eepInitMsg = DataEEInit();
	
	if (eepInitMsg == 1){
		aknControlData.pidCal = PIDEEP_PAGE_EXP; // Page Expired
	} else if (eepInitMsg == 6){
		aknControlData.pidCal = PIDEEP_MEMORY_CORR; // Memory Corrupted
	}
}

void loadEEPData(void){
	unsigned char i;
	
	for(  i = 0; i < 10; i++ )
	{
		// PID Gains
		pidControlData.P[i].shData[0]= DataEERead(PID_OFFSET+i*6);
		pidControlData.P[i].shData[1]= DataEERead(PID_OFFSET+i*6+1);
		pidControlData.I[i].shData[0]= DataEERead(PID_OFFSET+i*6+2);
		pidControlData.I[i].shData[1]= DataEERead(PID_OFFSET+i*6+3);
		pidControlData.D[i].shData[0]= DataEERead(PID_OFFSET+i*6+4);
		pidControlData.D[i].shData[1]= DataEERead(PID_OFFSET+i*6+5);
		
		// Way Points
		wpsControlData.lat[i].shData[0]= DataEERead(WPS_OFFSET+i*8);   
		wpsControlData.lat[i].shData[1]= DataEERead(WPS_OFFSET+i*8+1);      
		wpsControlData.lon[i].shData[0]= DataEERead(WPS_OFFSET+i*8+2);      
		wpsControlData.lon[i].shData[1]= DataEERead(WPS_OFFSET+i*8+3);      
		wpsControlData.hei[i].shData[0]= DataEERead(WPS_OFFSET+i*8+4);      
		wpsControlData.hei[i].shData[1]= DataEERead(WPS_OFFSET+i*8+5);      
		wpsControlData.typ[i]		  = (unsigned char)DataEERead(WPS_OFFSET+i*8+6);
		wpsControlData.val[i].shData   = DataEERead(WPS_OFFSET+i*8+7);         	
	}
	// load WP 11 that contains the GS location
	i = 10;
	wpsControlData.lat[i].shData[0]= DataEERead(WPS_OFFSET+i*8);   
	wpsControlData.lat[i].shData[1]= DataEERead(WPS_OFFSET+i*8+1);      
	wpsControlData.lon[i].shData[0]= DataEERead(WPS_OFFSET+i*8+2);      
	wpsControlData.lon[i].shData[1]= DataEERead(WPS_OFFSET+i*8+3);      
	wpsControlData.hei[i].shData[0]= DataEERead(WPS_OFFSET+i*8+4);      
	wpsControlData.hei[i].shData[1]= DataEERead(WPS_OFFSET+i*8+5);      
	wpsControlData.typ[i]		  = (unsigned char)DataEERead(WPS_OFFSET+i*8+6);
	wpsControlData.val[i].shData   = DataEERead(WPS_OFFSET+i*8+7);         	

	// Compute the waypoint count
	i = 0;
	while ((int)(wpsControlData.lat[i].flData) != 0 && i < 9 ) i++;{
		wpsControlData.wpCount = i;
	}
}
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

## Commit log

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2008-08-18 GPS message splitter working correctly
    [circBufferDriver.c]
2008-08-22 Startup point for bufferedUART.c. Corrected bug in Circular Buffer dsPIC implementation. Changed implementation of CircBuffer for dsPIC so it can have multiple instances without using malloc
    [apDefinitions.h, circBufferDriver.c]
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2008-08-26 Data Logger driver working on Port 2. First version of the communications protocol set in place
2008-08-27 Completion of GPS driver and Data logger. Communications protocol has 2 sentences, GPS and CPU Load
2008-08-27 Raw Sensor Data Logger implemented. Corrected break bug in the main switch statement in the comm protocol
    [apDefinitions.h, dataLogger.c]
2008-08-28 Started Interprocessor communication. Still not working
    [apDefinitions.h, dataLogger.c, interProcComm.c]
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2008-08-31 Interprocessor communication working with dummy data. Split model into Sensor and Control MCUs
2008-08-31 initial steps for full blown SPI IPC
    [apDefinitions.h, dataLogger.c, interProcCommMaster.c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]
2008-08-31 Nasty bug in sentence formation
    [apDefinitions.h, dataLogger.c]
2008-09-01 Fixed nasty bug in muxing signal to dataLogger
    [apDefinitions.h, dataLogger.c, interProcCommMaster.c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]
2008-09-03 Started Documentation of Comm Protocol, ground station is Next. Started the parser/decoder for the comm protocol
    [CommunicationsProtocol.xls]
2008-09-04 Most of the Communications Protocol described in the XLS sheet. Infinite loop bug in the Procol Decoder
    [CommunicationsProtocol.xls]
2008-09-04 Protocol decoder working. Now IPC NOT working :-S
    [CommunicationsProtocol.xls]
2008-09-05 Fully Working implementation of IPC and Protocol Decoding. Currently implemented three messages: 1,2 3
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2008-09-11 Inclusion of serial driver. Initial steps for motion of UAV in Google Earth
2008-09-11 Ready to start tests of Ground Station. Nothing has been debugged yet
    [CommunicationsProtocol.xls]
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2008-09-20 Bug corrections to Kalman Filter
2008-09-22 Inclusion of Gregg's complementary filter for attitude estimation. Added two new message sentences: Attitude and XYZ in LTP
    [CommunicationsProtocol.xls]
2008-09-28 Finally eliminated the 'missing byte' bug in the serial DMA. IPC fully working and tested with 4 messages: GPS, cpu status, Attitude, XYZ.
    [CommunicationsProtocol.xls]
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2008-10-21 Hunting bug in XYZ message. Checksum always fails
    [UPpal.cpp, protDecoDriver.c, protDecoder.c]
2008-10-23 Finally chased out XYZ strange bug. Procol working. Still error in interpreting XYZ data
    [dataLogger.c, protDecoDriver.c, protDecoder.c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]
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2008-10-24 Inclusion of GPS Dropouts in the model. Implementation of magneto pendular for attitude. Comparison of both modes
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2008-10-28 Initial modification to embed complementary filter
    [CommunicationsProtocol.xls]
2008-10-30 Initial steps for ground decoding from ground station
    [CommunicationsProtocol.xls]
2008-10-30 First complete tryout of the send/receive protocol. NOT WORKING
    [CommunicationsProtocol.xls]
2008-10-30 Chased out the bugs for the GS protocol. Kind-of-working :-)
    [protDecoder.c]
2008-10-31 Unknown bug in Sensor MCU
    [apDefinitions.h, dataLogger.c]
2008-10-31 Debugging weird error in filter
    [UPpal.cpp]
2008-11-02 Correction of ATAN2 bug in Simulink. Attitude working on bench; ready for cart-test
    [UPpal.cpp, apUtils.c]
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2008-11-06 Correction to open loop integration during GPS outages
    [UPpal.cpp, protDecoder.c]
2008-11-07 Ground tests partially successfull. Inclusion of all Sensor MCU messages
    [CommunicationsProtocol.xls]
2008-11-08 Major achievement, car test complete. Inclusion of time stamp in data. Live data logger corrected
    [UPpal.cpp, apDefinitions.h, dataLogger.c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]
2008-11-10 Inclusion of required components for the ground station. Plotting and parsing script
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2008-11-21 Hunting misterious bug in the way temperature is displayed
2008-11-22 Initialization of biases at boot time. Change of wxVb to use SOG and COG instead of XYZ from filter
2008-11-23 Inclusion of required blocks in Sensor MCU to enable the HIL switching mechanism
2008-12-01 Ironing out bugs for flight
    [UPpal.cpp, dataLogger.c, interProcCommSlave.c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]
2008-12-03 Still hunting the bug
    [interProcCommSlave.c]
2008-12-03 SPI Bug is gone. Circular buffer has been migrated to no Length data member. Ready to debug the failure
    [interProcCommSlave.c]
2008-12-04 Working version. Aparantly CB bug is gone. Need to check for longer time
    [interProcCommSlave.c]
2008-12-09 Finally got rid of Circular Buffer bug
    [interProcCommSlave.c, protDecoder.c]
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2008-12-09 Getting ready for slow data rate to SD card. Moved Checksum and AssembleMsg to APUtils.c
2008-12-12 Corrected Magnetometer reading bug
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2008-12-13 Sensor calibration and temperature compensation in place. Only need to change rate of raw data. Code ready to fly
2008-12-19 Logging of Pilot console commands ready to fly. Proven in messages, Ground Station and Logging. No SD Card logging yet
2008-12-19 Corrected bug in Static pressure, now it indicates meeters. Ready for second flight
2009-01-13 Modification of XLS file to include the PWM commands message
    [CommunicationsProtocol.xls]
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2009-01-14 Changed the way the global state structures are implemented. Getting ready for PWM commands
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2009-01-14 Finished first run of PWM messages. Needs to be implemented in Simulink
2009-01-14 Simulink Model ready to test new telemetry reporting architecture and PWM message
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2009-01-15 Added some missing files to repository
    [groundStationDriver.c]
2009-01-16 Inclusion of PWM mesasges to protocol description
    [CommunicationsProtocol.xls]
2009-01-16 Changed the Telemetry Serial port to COM2. Started using the TODO Bundle. Added mechanism to set and query PID gains
    [CommunicationsProtocol.xls]
2009-01-16 Slight Modification to the way messages regarding gains, limits and calibration are decoded. Inclusion of short values in float Union type to allow for storage and retrieval of 2-byte values for EEPR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
    [apDefinitions.h, apUtils.c, groundStationDriver.c]
2009-01-17 Communications protocol document update
    [CommunicationsProtocol.xls]
2009-01-17 Slight modifications and syntax error corrections
    [apDefinitions.h, apUtils.c, protDecoder.c]
2009-01-17 Minor corrections to apDefinitions. Included short field in the float union for EEPROM storage
    [apDefinitions.h]
2009-01-17 Sintax error corrections continue
    [apUtils.c, groundStationDriver.c]
2009-01-19 implemented aknowledge message in GS. Now it displays a message box on reboot
    [UPpal.cpp, apUtils.c, groundStationDriver.c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]
2009-01-19 Reboot message implemented. Revamped the GUI in the GS to have a better ordering of the tabs
    [UPpal.cpp, protDecoder.c]
2009-01-19 Working on the GS to get PID messages sent and AKN received
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2009-01-20 PID Messaging system working completely for PID Loop 1. PWM Messaging system fully working
2009-01-20 Finished polishing the GUI for the 10 PID loops. Preliminary tests work. Needs furhter testing
2009-01-21 Minor modifications to Protocol specifications XLS document
    [CommunicationsProtocol.xls]
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2009-01-21 Corrected bugs in GUI to correctly set the AKN message for PID gains. Added a conditional include to DEE.h
    [UPpal.cpp, apUtils.c]
2009-01-22 Squashed MAJOR bug in SPI comm. Added error handling to SPI IPC. Debuggin bug in PID messaging system. Not working yet
    [apUtils.c, groundStationDriver.c, interProcCommSlave.c]
2009-01-22 PID Gain configuration and storage in EEPROM fully working. Ready to merge to Master
2009-01-27 Inclusion of WP in protocol specs
    [CommunicationsProtocol.xls]
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2009-01-28 WP Configuration Working. Need to fix a minor layout in the GUI in the GS for better configuration of WP type. Need to add a way to send the GS location to the AP
    [UPpal.cpp, apUtils.c, groundStationDriver.c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]
2009-01-28 Changes to the Protocol Spec Document to reflect latest WP additions
    [CommunicationsProtocol.xls]
2009-01-29 Initial steps to get commands and AP Status working. Corrected the GUI bug that prevented from selecting WP Static type
    [UPpal.cpp, apDefinitions.h, apUtils.c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]
2009-02-02 Ready to start testing HIL replacement of attitude estimation
    [UPpal.cpp, dataLogger.c, protDecoder.c]
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2009-02-03 GS Software ready to test full HIL tx/rx including Attitude and Position replacement
    [UPpal.cpp]
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2009-02-09 Replaced for loop for memcpy in assambleMessage function
    [UPpal.cpp, apUtils.c]
2009-02-11 Included a way to notify of each MCU reset independently. Also simplified the init function for the Sensor MCU. Finally, added h files that were missing from some early C files
    [apDefinitions.h, apUtils.c, dataLogger.c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]
2009-02-12 Minor additions to the GUI. Change update rate of the GUI, added an overwrite log option and double reboot check
    [UPpal.cpp]
2009-02-26 Lateral and Longitudinal channels correctly tuned. Navigation implemented but not working. Some bug is making pitch oscilate
2009-03-02 Found and corrected bug in randow wp switching. Modified plot to look better
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2009-03-17 Started moving towards embedding the ap. Added support functions for navigation. Included trig functions for nav. Extensively modified the ap and nav code to protect against zero division and domain 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
    [UPpal.cpp, apUtils.c]
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2009-03-21 Implemented both MCU reset flags
    [UPpal.cpp, protDecoder.c]
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2009-03-29 Modified the GS GUI to display both MCU reboots
    [UPpal.cpp]
2009-03-30 Corrected some bugs and added minor features to HIL code in MCUs. HIL still not working
    [apDefinitions.h, apUtils.c, protDecoder.c]
2009-03-31 Corrected a plotting bug in Google Earth. Added value saving of WPs in GUI to ini file. Set low limit in WPs heigh to 350m
    [UPpal.cpp]
2009-04-02 Inner Loop working. Fixed all the bugs. Outer loop still not working. Modified the code to be able to use the biases message as a diagnostic tool
    [apUtils.c]
2009-04-03 Corrected MAJOR bug in how data is sent to HIL sim model, improved performance of the HIL considerably
    [UPpal.cpp, protDecoder.c]
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2009-04-03 Modified the way the timing is computed in the HIL Model. Need a way to correct for data outliers in PWM Commands
2009-04-07 Corrected a minor bug in how XYZ is reported in HIL. Added a new function to use the unused PWMCommand sentences to diagnose data. Lateral Channel is correctly tunned. Only the switching logic remain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
    [groundStationDriver.c]
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2009-04-30 L1 working in embedded. Getting ready to modify the HIL Sim model to include the failures capability
    [apUtils.c]
2009-04-30 Configuration of the HIL model to simulate aileron/rudder failures
2009-05-06 Still rudder failures not working
2009-05-06 Final version for rudder tolerance
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2009-05-14 Changed gain settings. Not working
    [magneto.c]
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2009-05-16 Changed the Sensor raw data to be signed. Initial steps for the CUBE driver. Still not working
    [adisCube.c, apDefinitions.h, apUtils.c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]
2009-05-18 ADIS Cube working with strange bug
    [adisCube.c]
2009-05-19 Looking for bug in code
    [adisCube.c]
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2009-05-19 Protocol spec document
    [CommunicationsProtocol.xls]
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2009-05-24 Complete redesign of the Sensor MCU model. Much more efficient and betetr commented. Ready to test new design
    [apDefinitions.h, apUtils.c, dataLogger.c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]
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2009-05-26 Added all hardware files including OrCAD schematics, OrCAD layout files, gerber files, and schematic pdfs. This is my first addition to the repository.
    [SLUGS_V2.DSN, slugs_v2.brd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]
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2009-06-09 Added the GroundStation Binary. Included the small control surface connection board schematic, layout and gerbers
    [ConnectionBoard.brd, ConnectionBoard.sch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]
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2009-06-29 Changed automatic changing to and from Automatic and Manual in the ground station. Included the correct labels for control surfaces
    [UPpal.cpp]
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2009-07-08 Corrected several bugs regarding transition from manual to automatic control of the UAV. Inner loop fully working in HIL. Outer loop needs debugging
    [adisCube.c, apDefinitions.h, interProcCommMaster.c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]
2009-07-09 Got complementary attitude Kalman position filters working on the dsPIC. Filter needs sign correction somewhere. not working yet
2009-07-11 Modified file to have 3D filter with startup init. Added ellipse correction to mags and accels
2009-07-11 Added PID anti-windup, Ellipse Correction, and First Order low-pass with initial conditions
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2009-07-13 Added all the required corrections for sensor calibration and signal conditioning. Added a watch block for the magnetometer block. Model ready to fly
    [apDefinitions.h, interProcCommMaster.c, magneto.c]
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2009-07-17 Corrected several bugs from previous flight. Implemented a software Delta-Sigma ADC to average succesive A2D readings. Doubled the wait time for magneto to boot
    [gps.c, magneto.c]
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2009-07-19 Corrected bugs in the new Cube driver. Ready for hadrware test
    [adisCube.c, apDefinitions.h]
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2009-07-22 Corrected bugs on the rudder limit. Greg included the 100Hz passthrough
    [apDefinitions.h]
2009-07-22 Fixed a bug in the reporting process of telemetry data, where on the ground two messages were lost
    [protDecoder.c]
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2009-07-23 Minor bug corrections in de-rotation of euler angles. Ready to fly for parameter tunning
2009-07-25 Found BUG in IC module trying to eliminate it
    [apDefinitions.h, circBufferDriver.c]
2009-07-27 Fixed the problem when transitioning from manual to ap and grabbing the wrong trim conditions. Outer Loop HIL is not working for some reason
    [apUtils.c]
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2009-07-29 Corrected som NANs bugs in the real time plots
    [UPpal.cpp, protDecoder.c]
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2009-08-04 Included the gain to scale lateral accel command. Corrected the POD rotation; it was missing a transpose. Gain scheduled L2 to change with groundspeed
    [apDefinitions.h]
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2009-08-06 Corrected the problem with the integrator windup . Added new integration block with reset and anti-windup
    [dataLogger.c]
2009-08-06 Replaced the old PID blocks with the newly developed ones
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2009-08-10 Added NAN protection all over the control MCU. Need to chase down the bug that is producing the 1 sample time NAN in navigation
2009-08-31 Added new files for latest hardware revision. Included ORCAD files, PDFs and Gerbers. Added MIT OpenSource license to all source code files
    [SLUGS_V2.DSN, SLUGS_V2_1.DSN, adis16350.psm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]
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2010-02-11 Repo organization starts: ACConection board ready
    [DrillFile.drl]
2010-02-23 Added link_board Altium project to the repository. This board sits between the groundstation and the autopilot and connects directly to the Xtend radio.
    [PcbLib1.PcbLib, board.PcbDoc, board.PrjPcb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]
2010-02-26 Repo Organization: Moved AC Connection Board to hardware directory
    [ConnectionBoard.brd, ConnectionBoard.sch]
2010-02-26 Added spreadsheets with the board parts list as required by Sierra Proto Express and a buying list for two Multiplex Mentor Airframes
    [BoardPartsList.xls, MentorAirframe.xls]
2010-03-06 Finished implementing new architecture for navigation. Same algorithm (Park, Deyst, How) but a completely different (better?) implementation. Currently broken. Starting the debug process
2010-06-09 Added the rotation table SolidWorks files. This design was done by Brandon Kinman at the UCSC ASL
    [Assembly.SLDASM, Drawing1.SLDDRW, Drawing2.SLDDRW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]
